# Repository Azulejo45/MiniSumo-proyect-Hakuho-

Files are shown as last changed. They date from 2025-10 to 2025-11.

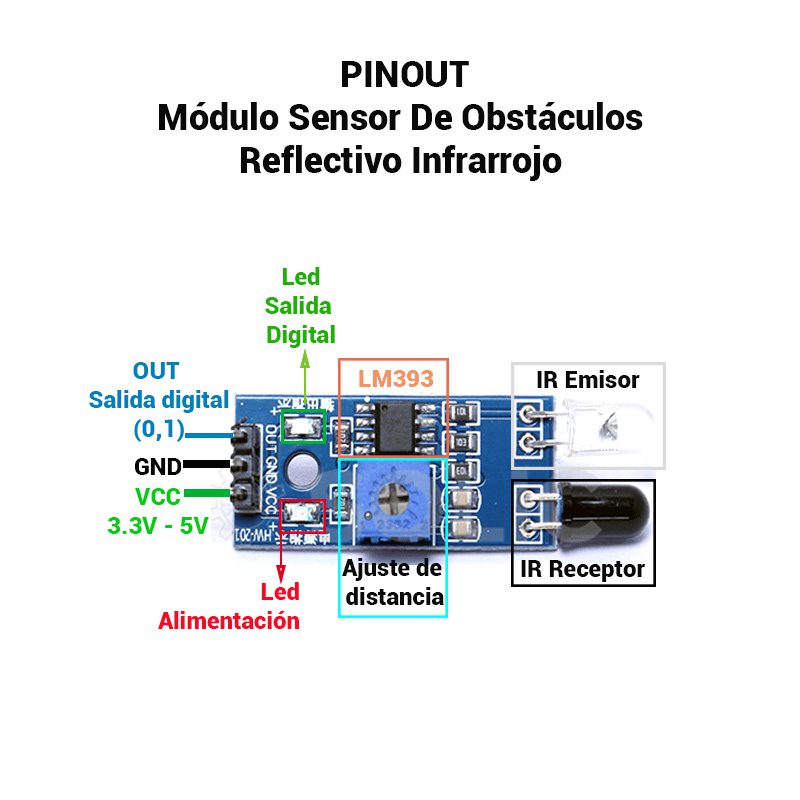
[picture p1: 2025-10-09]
Recursos/Datasheet AD-32.jpg

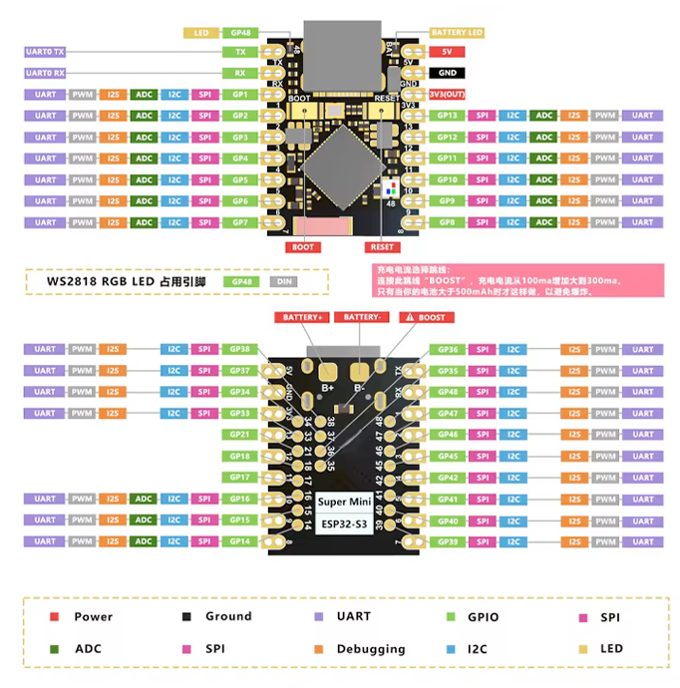
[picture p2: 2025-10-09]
Recursos/Datasheet Esp32.jpg

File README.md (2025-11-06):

### ┍━━━━━━━━━━━━»•» 🌺 «•«━━━━┑
#   ┕MiniSumo-Project-Hakuho┙        

### - Proyecto de mini sumo con la capacidad de ser controlado de manera bluetooth y automata. Equipado con 4 sensores:  2 laterales, 1 frontal y uno en la parte inferior, el de piso.
♥

## ..••°°━✦❘༻⋞ 〈 Autores  〉 ⋟༺❘✦━━°°••..

- ⋆ˊˎ-   ┌──༺♥༻❀**Velazquez Joaquim**❀༺♥༻──┐
  
- ⋆ˊˎ-  ↻ ◁ I**Perez Sebastían**I ▷ ↺3:11 ───ㅇ──── 5:25

- ⋆ˊˎ-   》＊•̩̩͙✩•̩̩͙*˚**Demian Ramirez**˚*•̩̩͙✩•̩̩͙*˚《

### *---02/10/2025---*

♥
## •*¨*•.¸¸☆*･ﾟ Especificaciones generales ﾟ･*☆¸¸.•*¨*•

˚₊· ͟͟͞͞➳❥ Dimensiones del robot: 10 cm x 10 cm x 4,5 cm.

˚₊· ͟͟͞͞➳❥ Consumo total: 7,4V.

˚₊· ͟͟͞͞➳❥ Corriente total: 800mA.

˚₊· ͟͟͞͞➳❥ Material de la carrocería: PLA.

˚₊· ͟͟͞͞➳❥ Peso (aproximado): 250g.
## ✭∞∞∞∞∞∞∞∞✭∞∞•,¸,.·' ✩ '·.,¸,•∞∞✭∞∞∞∞∞∞∞∞✭

♥
### ✎  (❁ᴗ͈ˬᴗ͈) ༉‧ ♡*.✧
## Objetivo del proyecto
### ✩°｡𓂃𓏧︶︶︶︶︶︶︶︶┈୨•♡•୧┈︶︶︶︶︶︶︶𓂃𓏧｡°✩
_El objetivo principal de este proyecto es poner a prueba lo aprendido en el transcurso del ciclo educativo y poder aplicarlo en el ensamblaje y preparacion de un robot modelo Mini-Sumo para que se encuentre en condiciones en poder participar en una competencia.
El Mini-sumo está implementado con sensores los cuales lo ayudarán en la detección de obstaculos y/o de un mini-sumo enemigo, utilizando su rampa para contraatacar hasta expulsarlo de la zona de combate._
_Además, el robot consta con un modo "remote control" (RC), esto está implementado con el sistema de bluetooth y wi-fi integrado en el ESP32._
### ✩°｡𓂃𓏧⌒⌒⌒⌒⌒⌒⌒⌒┈୨•♡•୧┈⌒⌒⌒⌒⌒⌒⌒⌒𓂃𓏧｡°✩

♥
### ∘₊✧───∘₊✧───•-•⟮ ◆ ⟯•-•───✧₊∘───✧₊∘
## ˗ˏˋ ꒰ **Este proyecto fue realizado con algunos componentes en donde se puede llegan a encontrar:** ꒱ ˎˊ˗

- Micro: Esp32 S3 super mini.
 > Memoria: 512 KB SRAM, 4 MB Flash.Conectividad: Wi-Fi 802.11 b/g/n (2,4 GHz).\
 > Bluetooth 5.0 LE (Low Energy).\
 > Alimentación: Funciona a 3,3 V con entrada USB-C de 5 V.

- Bateria de Lipo.
 > Almacenamiento: 7,4V.\
 > 2 celdas (3,7V por celda)
  
- Sensor de piso: TCRT5000.
 > Voltaje de operación: 3.3V-5V.\
 > Dimensiones: 31 mm × 13 mm × 2 mm.\
 > Rango de detección: 30° más amplio.

- Sensor detector de obstáculos: AD-32.
 > Voltaje de operacion: 3V-5.5V.\
 > Cantidad de pines: 4.\
 > Distancia de deteccion: 5 a 20mm.
 
- Motores: Micro motores Pololu 250RPM.
 > Dimensiones: 26x10x12mm.\
 > Voltaje de operacion: 6V.\
 > Torque maximo: 333Nm (Newton - metro).

- Puente H: DRV8833.
 > Dimensiones: 4 mm × 18,1 mm × 21,1 mm.\
 > Voltaje de operacion: 2.7V-10.8V.\
 > Corriente máxima de salida: 1,5A.
 ### ∘₊✧───∘₊✧──────✧₊∘───✧₊∘

♥
## ╔══✬✩══╡˚✧Componentes utilizados✧˚╞══✩✬══╗
- ˋ°•*⁀.¸➸ *Esp32 S3 super mini.*
- ˋ°•*⁀.¸➸ *Bateria de Lipo.*
- ˋ°•*⁀.¸➸ *TCRT5000.*
- ˋ°•*⁀.¸➸ *AD-32.*
- ˋ°•*⁀.¸➸ *Micro motores Pololu 250RPM.*
- ˋ°•*⁀.¸➸ *DRV8833.*
## ╚═══*+:｡ . ｡:+*═══✮❁•°❀°•❁✮═══*+:｡ . ｡:+*═══╝
/
/
/
/
/
♥
# Diseño del circuito

PCB MiniSumo

## Descripcion del funcionamiento

El minisumo utiliza sus varios sensores para guiarse, con dos ubicados en los costados; otro en la parte frontal. Cuando un objeto entra en el rango del sensor frontal, el minisumo avanza hasta chocar contra dicho objeto. Esto siempre se cumple hasta que se quite la orden.\
Cuando uno de los sensores en los costados detectan algo cerca, se posiciona para estar de frente al objeto, retrocediendo y girando en direccion paralela a este.

♥
Esquematico MiniSumo

## Layout de PCB



# Pasos a seguir para armar el mini-sumo
## ˚*•̩̩͙✩•̩̩͙*˚＊˚*•̩̩͙✩•̩̩͙*˚＊˚*•̩̩͙✩•̩̩͙*˚＊˚*•̩̩͙✩•̩̩͙*˚＊˚*•̩̩͙✩•̩̩͙*˚

### Primero elistaremos las herramientas necesarias para llevar a cabo la placa.
-Un recipiente\
-Percloruro\
-Una agujereadora\
-Una placa de cobre\
-Papel fotografico\
-Tinta Tonel\
-Una impresora(Para imprimir el diseño PCB)
-Cable USB-C (Para cargar el codigo.)

 ### -|preparación de la placa:

1. Descargar el archivo de PCB de "HakuhoNII.kicad_pcb" (YO NO LO DESCARGO PORQUE YA LO TENGO XDDDD).
2. Imprimir el PCB en una hoja fotográfica (como lo son las hojas de revista) con tinta "tonel".
3. Proceda a planchar el PCB a la placa del lado del cobre.
4. Revisar que el diagrama del PCB se haya pegado correctamente retirando la hoja fotográfica y cualquier excendete de esta(Utilice agua para remover con facilidad el papel).
5. Sumergir la placa en un recipiente con percloruro.
6. Dejarlo descansar un tiempo(Resivar periodicamente el cobre de la placa)
7. Cuando el cobre se haya disuelto y solo quede el diseño, retirarlo con CUIDADO(Es un liquido corrosivo;dificil de quitar de la ropa).
8. Limiparlo la placa con agua para quitar el excedente de percloruro.

 ### -|Soldar los componentes en la placa ya hecha en el siguiente orden:
 
1. Puentes
2. Boton
3. Capacitores
4. Switch
5. Pineras
6. Borneras
7. regulador

 ### Medidas de seguridad.

-El percloruro es un tanto corrosivo, capáz de manchar con facilidad la ropa y otra prendas.\
-Cuando vaya a hacer agujeros en la placa, tiene que ser en una superficie solida. Es probable que la placa pueda salir dispara en una base dispareja o inquieta.\
-Mientra planche, este atento a no quemar completamente el papel. Podria causar un incendio.

### Tipo de soldadura/ensamble
Todos los componentes deben fijados a la placa mendiante "soldadura de ola", el cual se utiliza para componentes de orificio pasante(THT). Los componentes debe ser introducidos desde el lado de la placa lisa y sin diseño,para ser soldados en el cobre que se encuentra del otro lado.
En las pineras que estan direccionadas en horizontal, se debe colocar el ESP32(integrado).
En la pineras que se encuentran en vertical, el DRV8833.

### -|Carroceria

1. Descargar el modelo 3D de la carroceria.
2. Descargar un modelo 3D de dos braquets y 2 ruedas con un radio de 20mm.
3. Imprimir ambos archivos.
4. Comprar cuatro tornillos para tuerca M3, 6 tuercas M3 y 2 prisioneros M3.
5. Unir la carroseria con los braquets mediante 4 tornillos M3 y 4 tuercas M3.

### -|Codigo

El codigo establece las instrucciones que ejecutara el integrado para poder accionar y manejar al mini-sumo.\
este es bastante simple y considera los 4 sensores teniendo en cuenta que:

- No debe salir del tatami.
- Debe atacar y empujar al otro mini-sumo fuera del area.
- Esquivar al mini-sumo rival cuando se le de la orden.

#### -|Compilacion/Carga

Cuando la placa ya este monatada, se utilizara un cable USB tipo C para conectar el integrado(ESP32) a un ordenador. Mediante el programa [Arduino IDE](https://www.arduino.cc/en/software). Copie el codigo que se encuentra en este repositorio y pueguelo en el programa. En el apartado superior encontrara 4 botones.\
El primero es para verificar si el programa tiene errores\
El segundo es para subir el codigo al integrado\
El tercero no es importante para esto.\
El cuarto es para poder seleccionar la placa y el puerto\
En este ultimo, busque el siguiente modelo: ESP32_S3_SUPER_MINI, y seleccionelo. En caso de no encontrarlo, use el "ESP32 S3 DEV MODULE". Junto a eso, seleccione el puerto USB por el cual esta conectado a su ordenador(Se cuenta de izquierda a derecha).\
Ahora, verifique el codigo por el primero boton de la parte superior. Si marca algun error, copie el codigo entero de nuevo y vuelva a pegarlo./
Una vez verificada la funcionalidad del codigo, utilice el segundo boton presente para poder subir el codigo al integrado de la placa. Si hay alguno otro error durante este proceso, consulte internet.

#### -[Librerias
Para poner librerias, dirigase al lateral izquierdo de la interfaz de Arduino IDE, y seleccione el tercer boton(Que contiene un simbolo con libros).
En el buscador de esta nueva pagina, encuentre las siguientes librerias:
-AdaFruit_NeoPixel.h

#### -[Datasheets/Referencias
-[AD-32](Recursos/Datasheet AD-32.jpg)

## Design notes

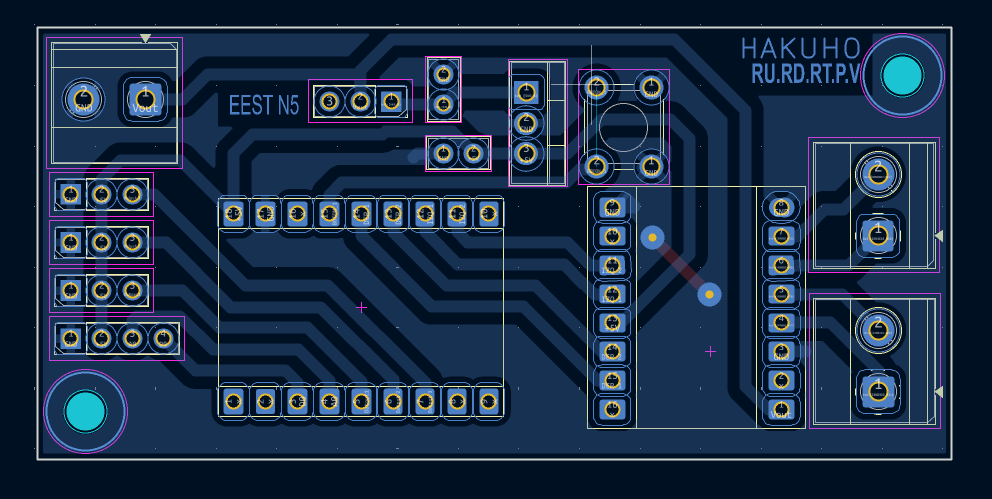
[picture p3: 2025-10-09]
Docs/PCB MiniSumo.png

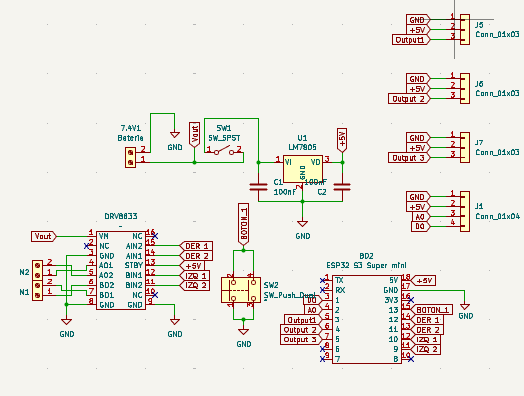
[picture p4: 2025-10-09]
Docs/Esquematico MiniSumo.png

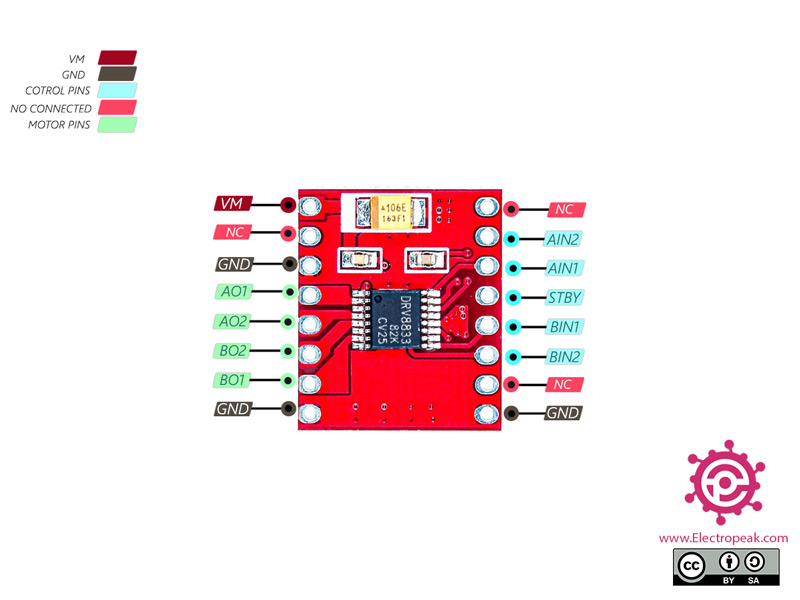
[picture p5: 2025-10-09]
Recursos/Datasheet_DRV8833.jpg

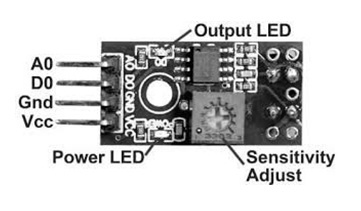
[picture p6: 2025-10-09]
Recursos/Datasheet_TCRT5000.jpg

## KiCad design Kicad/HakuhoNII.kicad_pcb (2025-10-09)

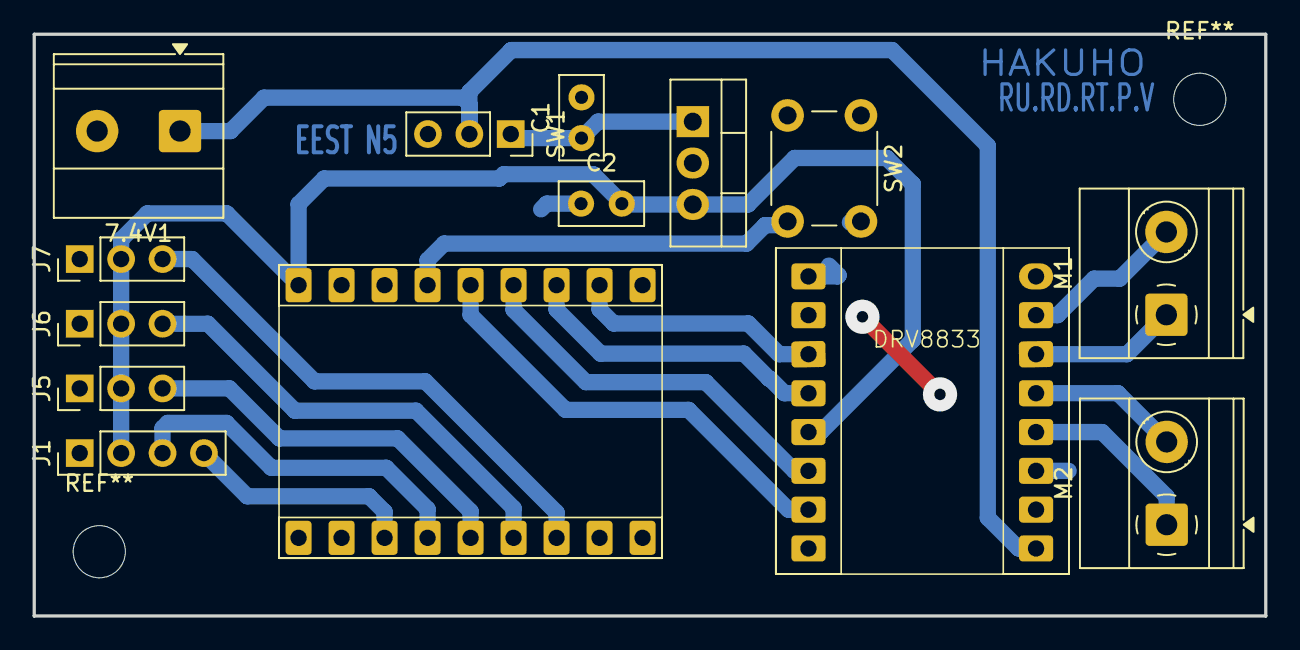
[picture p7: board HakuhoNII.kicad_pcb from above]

Board: 2 copper layers, 75.5 x 35.7 mm, 14 parts (0 on the bottom side), 18 nets.

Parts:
7.4V1: Bateria; TerminalBlock_Phoenix_MKDS-1,5-2-5.08_1x02_P5.08mm_Horizont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
BD2: ESP32 S3 Super mini; ESP32 S3 SuperMini
C1, C2: 100nF; C_Disc_D5.0mm_W2.5mm_P2.50mm
DRV8833: drv8833
J1: Conn_01x04; PinHeader_1x04_P2.54mm_Vertical
J5, J6, J7: Conn_01x03; PinHeader_1x03_P2.54mm_Vertical
M1, M2: Screw_Terminal_01x02; TerminalBlock_Phoenix_MKDS-1,5-2-5.08_1x02_P5.08mm_Horizont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
SW1: SW_SPST; PinSocket_1x03_P2.54mm_Vertical
SW2: SW_Push_Dual; SW_PUSH_6mm
U1: LM7805; TO-220-3_Vertical

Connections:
+5V: BD2.18 (5V), C2.2, DRV8833.13 (STBY), J1.2, J5.2, J6.2, J7.2, U1.3 (VO)
A0: BD2.4 (2), J1.3
BOTON_1: BD2.15 (13), SW2.2
D0: BD2.3 (1), J1.4
DER 1: BD2.14 (12), DRV8833.15 (AIN2)
DER 2: BD2.13 (11), DRV8833.14 (AIN1)
GND: 7.4V1.2, BD2.17 (GND), C1.2, C2.1, DRV8833.3 (GND), DRV8833.8 (GND), DRV8833.9 (GND), J1.1, J5.1, J6.1, J7.1, SW2.1, U1.2 (GND)
IZQ 1: BD2.12 (10), DRV8833.12 (BIN1)
IZQ 2: BD2.11 (9), DRV8833.11 (BIN2)
unnamed: DRV8833.4 (AO1), M2.1
unnamed: DRV8833.5 (AO2), M2.2
unnamed: DRV8833.7 (BO1), M1.2
unnamed: DRV8833.6 (BO2), M1.1
unnamed: C1.1, SW1.1 (A), U1.1 (VI)
Output1: BD2.5 (3), J5.3
Output 2: BD2.6 (4), J6.3
Output 3: BD2.7 (5), J7.3
Vout: 7.4V1.1, DRV8833.1 (VM), SW1.2 (B)

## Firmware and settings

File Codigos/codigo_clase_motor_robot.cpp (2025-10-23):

class Motor {
  private:
    int _INA;
    int _INB;

    void avanzar(int pwm) {
      analogWrite(_INA, pwm);
      analogWrite(_INB, 0);
    }

    void retroceder(int pwm) {
      analogWrite(_INA, 0);
      analogWrite(_INB, pwm);
    }

    void detener() {
      analogWrite(_INA, 0);
      analogWrite(_INB, 0);
    }

  public:

    Motor(int pinMotorA, int pinMotorB) {
      _INA = pinMotorA;
      _INB = pinMotorB;
      pinMode(_INA, OUTPUT);
      pinMode(_INB, OUTPUT);
    }

    void mover(int velocidad) {
      if (velocidad > 0) {
        avanzar(velocidad);
      } else if (velocidad < 0) {
        retroceder(velocidad * (-1));
      } else {
        detener();
      }

    }
    void info() {
      Serial.println("los pines asignados a los motores son;");
      Serial.print("INA:");
      Serial.println(_INA);
      Serial.print("INB:");
      Serial.println(_INB);
    }

};

class Robot {
  private:
    Motor _motorIzq;
    Motor _motorDer;
    int _velocidad = 255;

  

  public:
    Robot(int InA1, int InB1, int InA2, int InB2){
      Motor motorIzq = Motor(InA1, InB1);
      Motor motorDer = Motor(InA2, InB2);

      _motorIzq=motorIzq;
      _motorDer=motorDer;
    }


    void mover(int velocidad, int velocidad2) {
      _motorIzq.mover(velocidad);
      _motorDer.mover(velocidad2);

    }

    void info(){
      _motorIzq.info();
      _motorDer.info();
    }  
};

Robot robot = Robot(9, 10, 11, 12);

void setup() {
  Serial.begin(9600);
  robot.info();
}

void loop() {

}
